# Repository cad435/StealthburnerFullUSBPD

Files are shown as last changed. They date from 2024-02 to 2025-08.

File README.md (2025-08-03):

## Before you download:
 - Update 2024-05-16: I implemented the new and EMI-improved toolhead-boards. However, the "new-EMI" feeders are untested right now. As it is working, I'll only upload the EMI-improved toolhead for now. While manufacturing the new toolheads I also discovered that some of the STM32F072 MCUs I used, are lacking pin 1 markers. It looked to me as if they where sanded down and re-marked (yes I bought them from Aliexpress). I'm not sure if the new EMI-improving did the trick or if some of the MCU's where just faulty. However I do like the new EMI-protection features, so it definately was not a bad investment.
 - Update 2024-07-28 The New Toolheads, together with the "old" Feeders did print for nearly 100h without a single connection-loss. I consider that setup **tested and confirmed working**. A new 3D-Printer in my local makerspace is built right now which will use a "new-EMI" feeder, so that will be also tested in the future.
 - Update 2025-08-02: I now face a different Problem with the setup. **This does affect NEMA14 (round) Steppers together with TMC2130-Drivers.** Standalone-Driver mode is working. Details see here: https://klipper.discourse.group/t/hunting-down-strange-issue-with-extruder-motor/24010. As mentioned by mykepredko on that forum the transistor for heater switching (Q3) is very close on spec as well as obsolete. It is therefore replaced with a CSD17552Q3A, that is well defined within the 3.3V Gate-Voltage.

# StealthburnerFullUSBPD
Two PCB's to connect a Voron Stealthburner Toolhead via USB-PD providing both power and data.

**This has compliant USB-C PD communication, this is not a "hacky" solution where I just shove 20V over the Power-Lines!** <br/>

You can actually charge your Phone, Power your USB-Soldering Iron or whatever you like with it :) <br/>
You can also just use the Feeder Board for whatever non-3D-Printer related USB-PD circuitry you like <br/>

This is aimed at people which are either having some kind of toolchanging system (like me) or are - for whatever reason - changing their toolheads often. Upsides of this project compared to CAN: One cable does it all. Plug it in, it'll work. Well and of course its for people who think USB-C PowerDelivery is cool...<br/><br/>

Konzept_V1 1

Out of my latest Project (Voron 2.4 with toolchanger) I felt the need to simplify connecting Stealthburner-Toolheads to the printer. USB-C PowerDelivery seems suitable. Although it'll only provide 20V to the Toolhead instead of the 24V, it should be good enough.<br/>

I asked around at the Voron-Discord (May 2023), only to find out that there was an attempt by Mellow, but it was taken out of the market. So I sat down and created my own.<br/>

The Project consists of 2 Boards:
 - The "Feeder" PCB which basically integrates some step-Down converter and a USB-PD source IC's
 - The "Toolhead" PCB which consists of an MCU and the neccessary hardware to run fans, heaters, thermistors and the like. <br/><br/>

<p align="center">
 
</p>
<br/><br/>
--> If you use a 4-port USB-Hub, use a half-decent one. I had bad experiences with the 3€ ultra-cheap hubs from Aliexpress, I'm running on a (cheap) Anker-Hub smoothly now. <br/>
<br/>

**Note** that I designed it to be used with 12V Fans (partly because I have loads of 12V Fans laying around). As you need all available airflow you can get, using 12V Fans with 12V seems a better Idea to me that using 24V fans with only 20V as this would mean loosing some power. If the interest is great enough I might add a stepup circuitry to provide 24V for the fans. I don't think its a good idea to step up heater-cartridge voltages as well, as this would mean I need to supply about 3A of current with a step up which generally will generate a considerable amout of heat (same goes for stepping down 20V to 12V). <br/>
<br/>

As of now, the PD power provider IC claim to use e-mark detection for the cables. <br/>
<br/>

Using 24V/40W heater cartridges with 20V will decrease power consumption to about 30W wich (I guess) should be enough for the standard Voron user (not enough though for High-Speed/High-Flow printing etc). That leaves 30W for the stepper-motors, fans etc. (should be plenty enough). Also there are higher power cartridges out there which'll increase power. <br/>
<br/>

**Comment on the Relay switching 5V AUX into the Powerpath:**<br/>
This is actually one of the biggest features of the board - another level of protection for avoiding damage to the printer and possibly other things.
If the heater switching-FET fails and shorts out (zero resistance, actually not uncommon on FET's), the cartridge would heat up indefinately until it fails, ignites or whatever it'll happen. Klipper can't do anything against it, because it will have no hardware controll over the FET and the Heater anymore.<br/>

UNLESS you have another switch to cut off the power - which comes in form of the FET Q1. It'll get switched off from klipper, as Klipper is able to disable the PD-Chip, therefore cutting power completely. However, we don't want to cut power completely, otherwise we can't talk to our MCU anymore an therefore would not be able to restart klipper. So the relay also switches, redirecting the powerpath around the PD-Chip from the "default" Stepdown (5V) to the toolhead. So we just "switch" power to another safe Level (5V). With 5V the heater doesn't have enough power to get seriously hot (I tested, it merely gets 50C hot).

Licensed under Open Source Hardware Association license https://www.oshwa.org/definition/

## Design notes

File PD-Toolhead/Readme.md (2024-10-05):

Update 2024-10-05: I accidentlly left R7 and R8 as 100R series resistance for the USB-Lines. This seemes to be working good for my main Printer <br>
For another setup however, I encountered problems. After a while I found 100R to be too much resistance. Therefore I replaced it with 0R default. <br>
If you find yourself to have random disconnects I advice you to increase those values (20R should be enough!) <br>
However I believe that the 2.2kR@100Mhz Common-Mode chocke (FL1) should be more than enough. <br> <br>

I found it working with all the Ferrite beads (L1/L4/L5) beeing only ~300R@100Mhz, as well as the common-mode choke beeing just ~600R@100Mhz. <br> <br>

Use two M2 brass inserts on the 2 holes beside the USB-C Connector. <br> <br>



The holes where the "unknurled" shoulder is fitted is 3.1mm in diameter 
Brass inserts I used are sold as "OD=3.5mm, Lenght=3mm". The critical measurement is denoted as "dk" in the picture below.



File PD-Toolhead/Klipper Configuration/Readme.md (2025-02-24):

# Klipper Configuration

Inside the provided Klipper_Toolhead.cfg there are only the lines written down which are tied to the hardware. <br>
Anything else (PID values, min temp, max temp for example) is setup specific. See https://www.klipper3d.org/Config_Reference.html for aditional information<br>

For the compile config, consider setting PB9 in GPIO pins (see Image below). <br>
This will spin up the fan connected to the bottom fan-connector (usually the fan for the Heatsink!) <br>
If anything happens during the print and the printer changes into error-mode, then your hotend (more specific the coldend/heatsink) will not overheat.

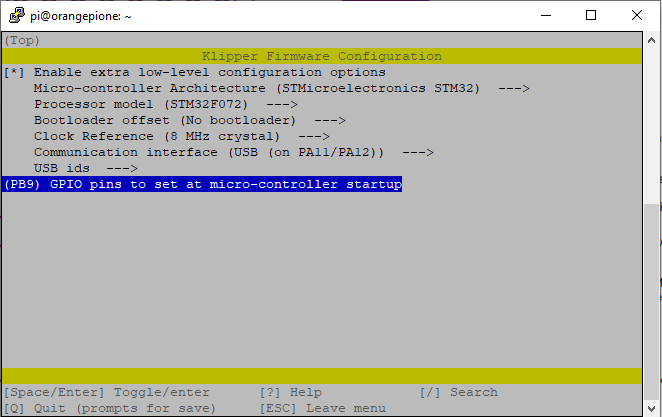
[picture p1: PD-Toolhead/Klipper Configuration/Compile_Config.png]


---

## Flashing with KIAUH v6:
KIAUH v6 has the ability to save compile configs.
 - download pd-hotend-stm32f072.config
 - place it inside /home/usr/klipper-kconfigs/ folder<br>
    (replace usr with your klipper user. On a standard installation this would be "pi" --> /home/pi/klipper-kconfigs/)
 - restart KIAUH v6 and navigate to the "Advanced"-Menu to get the firmware flashing Menu
 - when try to build or build+flash KIAUH should present you the option to load the config.

You also don't have to place the board in bootloader mode anymore. When flashing with KIAUH just select "connected via USB". The flash utility of KIAUH will place the board into bootloader-mode on its own. <br>
I'm not exactly sure since when this is possible. My setup runs with KIAUH v6 and Klipper v0.12.0. <br><br>

Be aware, that KIAUH may state a failed flash although flashing actually succeeds.<br>
Inside your command-Line you are looking for the lines:
```
[...]

Download        [=========================] 100%        36988 bytes
Download done.
File downloaded successfully
Submitting leave request...

[...]

```

See this post for additional reference:
https://github.com/dw-0/kiauh/issues/545#issuecomment-2395065270

---

## "Legacy" Flashing:

Hold down the "BOOT" button (see Pin Description PDF), than press the RESET Button. The Toolhead will be accessible via ST's USB-Hardware Bootloader in DFU. Use "USB (DFU mode)" option in KIAUH.

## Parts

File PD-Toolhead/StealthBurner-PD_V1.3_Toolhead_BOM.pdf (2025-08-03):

Comment | Description | Value | Designator | Footprint | Quantity
LM1117IMPX-3.3/NOPB | +3,3V LDO LM1117MP-3.3 | | A1 | SOT230P700X1.80-4N | 1
100nF | CAP-CER 100n 50V 10% SMD 0603 X7R | | C1, C2, C3, C4, C5, C19, C20, C23, C24, C27, C30 | CAPC1608X0.95N_0603 | 11
1µF | CAP-CER 1u 16V 10% SMD 0603 X7R | | C6, C7, C8, C17, C25, C26 | CAPC1608X0.95N_0603 | 6
10µF | CAP-CER 10u 25V 10% SMD 1206 X7R | | C9, C13, C14, C15, C16, C18, C21, C22, C31 | CAPC3216X1.80N_1206 | 9
100µF | CAP-ELC 100u 25V 20% SMD D6.3mm H7.7mm R4.4mm | | C10 | CAPAE660X8.00N_D8 | 1
18pF | CAP-CER 18p 50V 5% SMD 0603 C0G | | C11, C12 | CAPC1608X0.87N_0603 | 2
100pF | CAP-CER 100p 50V 5% SMD 0603 C0G | | C28, C29 | CAPC1608X0.87N_0603 | 2
SS1FL3HM3/H | DIO-SKY 30V 420mV 1A SMD DO-219AB SS1FL3HM3/H | | D1, D2 | SODFL3718X1.08N_DO-219AB | 2
2 Pin male | 2 Pin male | | FAN0, FAN1, Thermistor | JST_B2B-XH-A(LF)(SN) | 3
2.2kR @ 100MHz / 1206 | 2 Line Common Mode Choke 1206 | | FL1 | Common Mode Choke 1206 | 1
Terminalblock X2 | | | Heater | TerminalblockX2 | 1
JP1X4 | 4 Pin PFOSTENSTECKER, Fastermaß 2,54mm | | I2C, P2, P3 | P1x4-R2.54-X0.67 | 3
STM32F072C8T6 | Integrated Circuit | | IC1 | QFP50P900X900X160-48N | 1
ME3116 | 1A up to 40V Input Step-Down DC/DC Regulator | | IC2, IC3 | SOT23-6 | 2
Switch Black | Tactile Switch | | J1 | Tactile_SW_2Pins | 1
Switch Red | Tactile Switch | | J2 | Tactile_SW_2Pins | 1
USB 3.1 C Receptacle | USB 3.1 Type C Receptacle Horizontal THR WR-COM | | J3 | C165948 | 1
Ferrite_Bead | Ferrite_Bead | 600R @ 1MHz | L1, L4, L5 | 0603 | 3
Inductor | Inductor | 4.7uH/1.7A/1210 | L2, L3 | 5.2x4mm | 2
LED-0603 GN LC | LED WÜRTH 2mA 150060VS75000 | | LD1, LD2, LD3 | LEDC1608X0.80N_0603 | 3
3 Pin male | 3 Pin male | | LED | JST_B3B-XH-A(LF)(SN) | 1
JST-XH | 4 Pin male | | MOT | JST_B4B-XH-A(LF)(SN) | 1
Marker IPC7351 | Fiducial Marker IPC7351 Diameter 1.5mm, Clearance Diameter 3mm | | MP1, MP2, MP3, MP4, MP5, MP6 | PCB-Marker_IPC7351 | 6
JP1X3 | 3 PIN PFOSTENSTECKER, Rastermaß 2,54mm | | P4 | P1x3-R2.54-X0.63 | 1
CSD17552Q3A | N-MOSFET LOW RDSon | | Q1, Q2, Q3 | SON67P300X300X1.00-9N | 3
10k | RES 10k 1% 100mW TK100 SMD 0603 G | | R1, R2, R3, R10, R18, R20, R21, R26, R27, R32, R33, R34, R36 | RESC1608X0.55N_0603 | 13
0 | RES 0R 5% 100mW TK100 SMD 0603 G | | R6, R7, R8 | RESC1608X0.55N_0603 | 3
100k | RES 100k 1% 100mW TK100 SMD 0603 G | | R9, R25 | RESC1608X0.55N_0603 | 2
1k | RES 1k 1% 100mW TK100 SMD 0603 G | | R11, R12, R35 | RESC1608X0.55N_0603 | 3
100 | RES 100R 1% 100mW TK100 SMD 0603 G | | R14, R16, R17, R24, R37, R38 | RESC1608X0.55N_0603 | 6
470k | RES 470k 1% 100mW TK100 SMD 0603 G | | R22 | RESC1608X0.55N_0603 | 1
680R | RES 680R 1% 100mW TK100 SMD 0603 G | | R23 | RESC1608X0.55N_0603 | 1
4.7k | RES 4k7 1% 100mW TK100 SMD 0603 G | | R28, R29, R30 | RESC1608X0.55N_0603 | 3
P1X6-R2.54mm-V-X9.5mm | P1X6-R2.54mm-V-X9.5mm-Modu II Stiftleiste | | SPI | P1X6-R2.54-V-X9.5 | 1
TMC2130BREAKOUT | | | TMC1 | TMC2130BREAKOUT | 1
CH224K | USB PD and Other Fast Charging Protocol Sink Controller | Value | U1 | ESSOP100P600X180_E P-11N | 1
XTAL_8MHz | Crystal | | Y1 | SMD-3225_4P | 1

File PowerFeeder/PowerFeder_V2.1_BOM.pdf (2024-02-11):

Comment | Description | Value | Designator | Footprint | Quantity
100µF | CAP-ELC 100u 25V 20% SMD D6.3mm H7.7mm R4.4mm | | C1, C6, C17 | CAPAE660X8.00N_D8 | 3
100nF | CAP-CER 100n 50V 10% SMD 0603 X7R | | C4, C7, C8, C9, C10, C11, C12, C13 | CAPC1608X0.95N_0603 | 8
10µF | CAP-CER 10u 25V 10% SMD 1206 X7R | | C14 | CAPC3216X1.80N_1206 | 1
V8PAM10S | DIO-SKY 100V 840mV 8A SMD DO-221BC-2 V8PAM10S | | D1, D3, D5 | DO-221BC | 3
6.3A 250V | NResettable, 6.3A, 250V, SMD UMT250 | | F1 | FUSC10030X3.00N | 1
120 | FERRIT-BEAD-120R-3A-1206 | | FB1, FB2 | INDC3216X1.30N_1206 | 2
USB 3.1 C Receptacle | USB 3.1 Type C Receptacle Horizontal THR WR-COM | | J1, J2 | C165948 | 2
Terminalblock X2 | | | J3, J4, J5 | TerminalblockX2 | 3
Inductor | Inductor | 15uH | L1 | 12x12_L-Footprint | 1
Marker IPC7351 | Fiducial Marker IPC7351 Diameter 1.5mm, Clearance Diameter 3mm | | MP1, MP2, MP3, MP4, MP5, MP6 | PCB-Marker_IPC7351 | 6
NCE3080 | NCE N-Channel Enhancement Mode Power MOSFET | | Q1 | NCE3080 | 1
SI2318CDS-T1-GE3 | N-MOSFET SI2318CDS-T1-GE3 | | Q2, Q3 | SOT95P240X1.10-3N_SOT-23 | 2
0 | RES 0R 250mW SMD 1206 G | | R1, R14, R19, R24, R38 | RESC3216X0.65N_1206 | 5
1.5k | RES 1k5 1% 100mW TK100 SMD 0603 G | | R8, R12, R18, R20 | RESC1608X0.55N_0603 | 4
Res | Resistor | 5m | R13 | R2512 | 1
100k | RES 100k 1% 100mW TK100 SMD 0603 G | | R15, R16, R23 | RESC1608X0.55N_0603 | 3
33K | RES 33k 1% 100mW TK100 SMD 0603 G | | R17 | RESC1608X0.55N_0603 | 1
10k | RES 10k 1% 100mW TK100 SMD 0603 G | | R22, R26, R27, R28, R29, R31, R32, R33, R34, R35, R36 | RESC1608X0.55N_0603 | 11
Relay, SRA-xVDC-CL | | | S1 | SRA-24VDC-CL | 1
RT8289 | Buck Step Down Regulator with 5.5 to 36 V Input and 1.23 to 31 V Output, -40 to 125 degC, 8-Pin SOIC (D), Green (RoHS & no Sb/ Br) | | U2 | SOP8-EP | 1
TPS25740B | | | U3 | QFN-24_EP | 1

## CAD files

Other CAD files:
PD-Toolhead/USB_Cable_Holder.f3z

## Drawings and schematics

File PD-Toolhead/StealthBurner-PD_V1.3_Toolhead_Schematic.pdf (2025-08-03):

C10
100µF

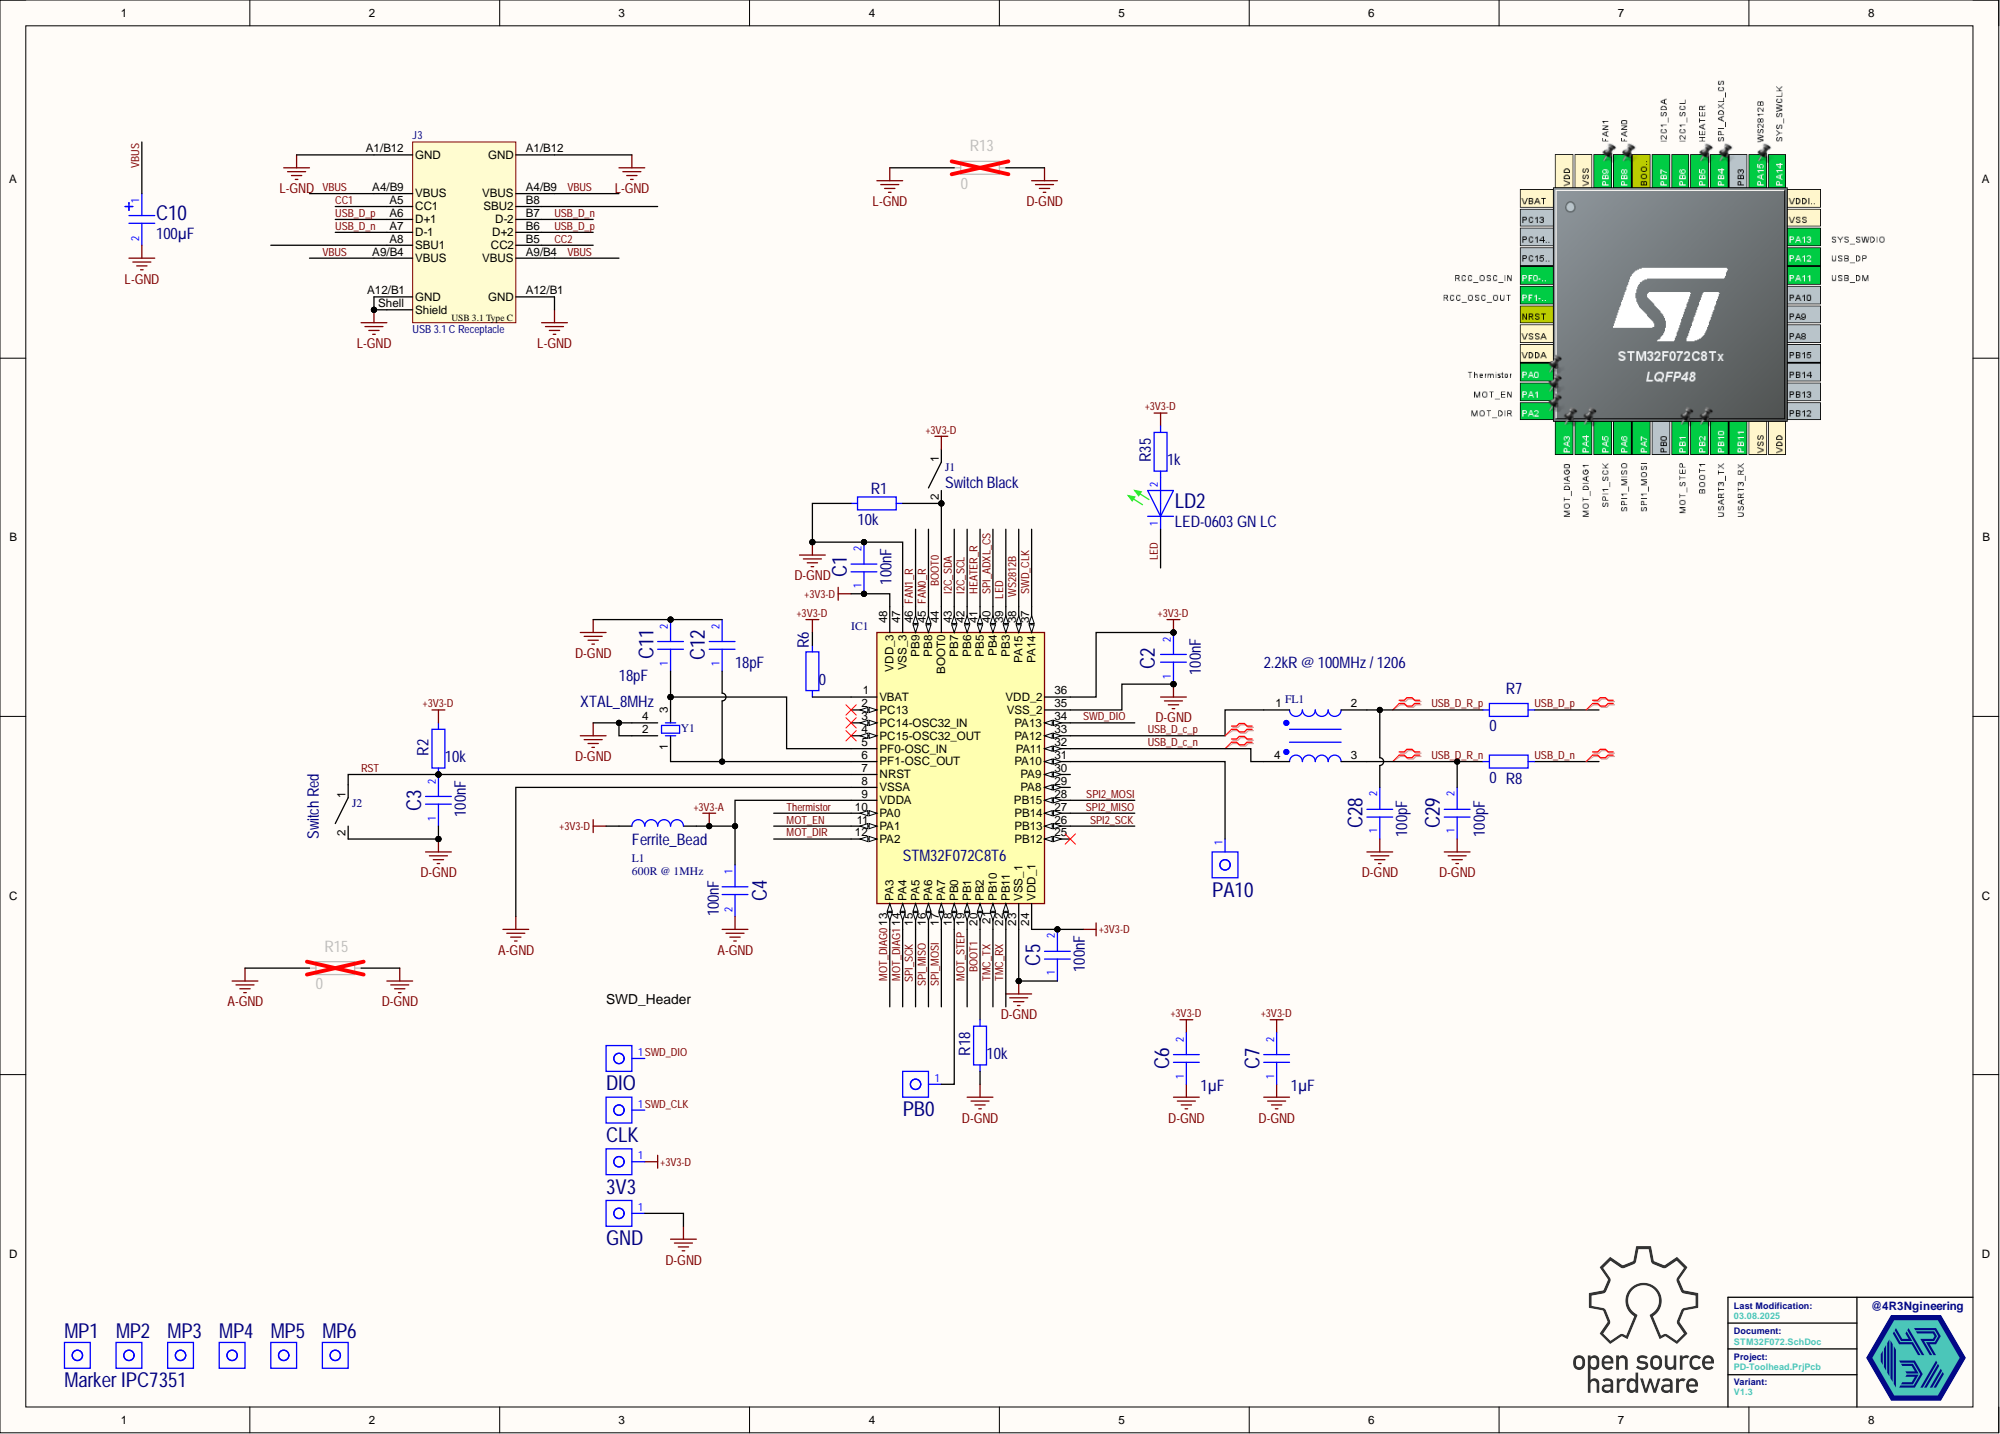
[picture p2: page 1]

## Ferrite_Bead +3V3-TMC

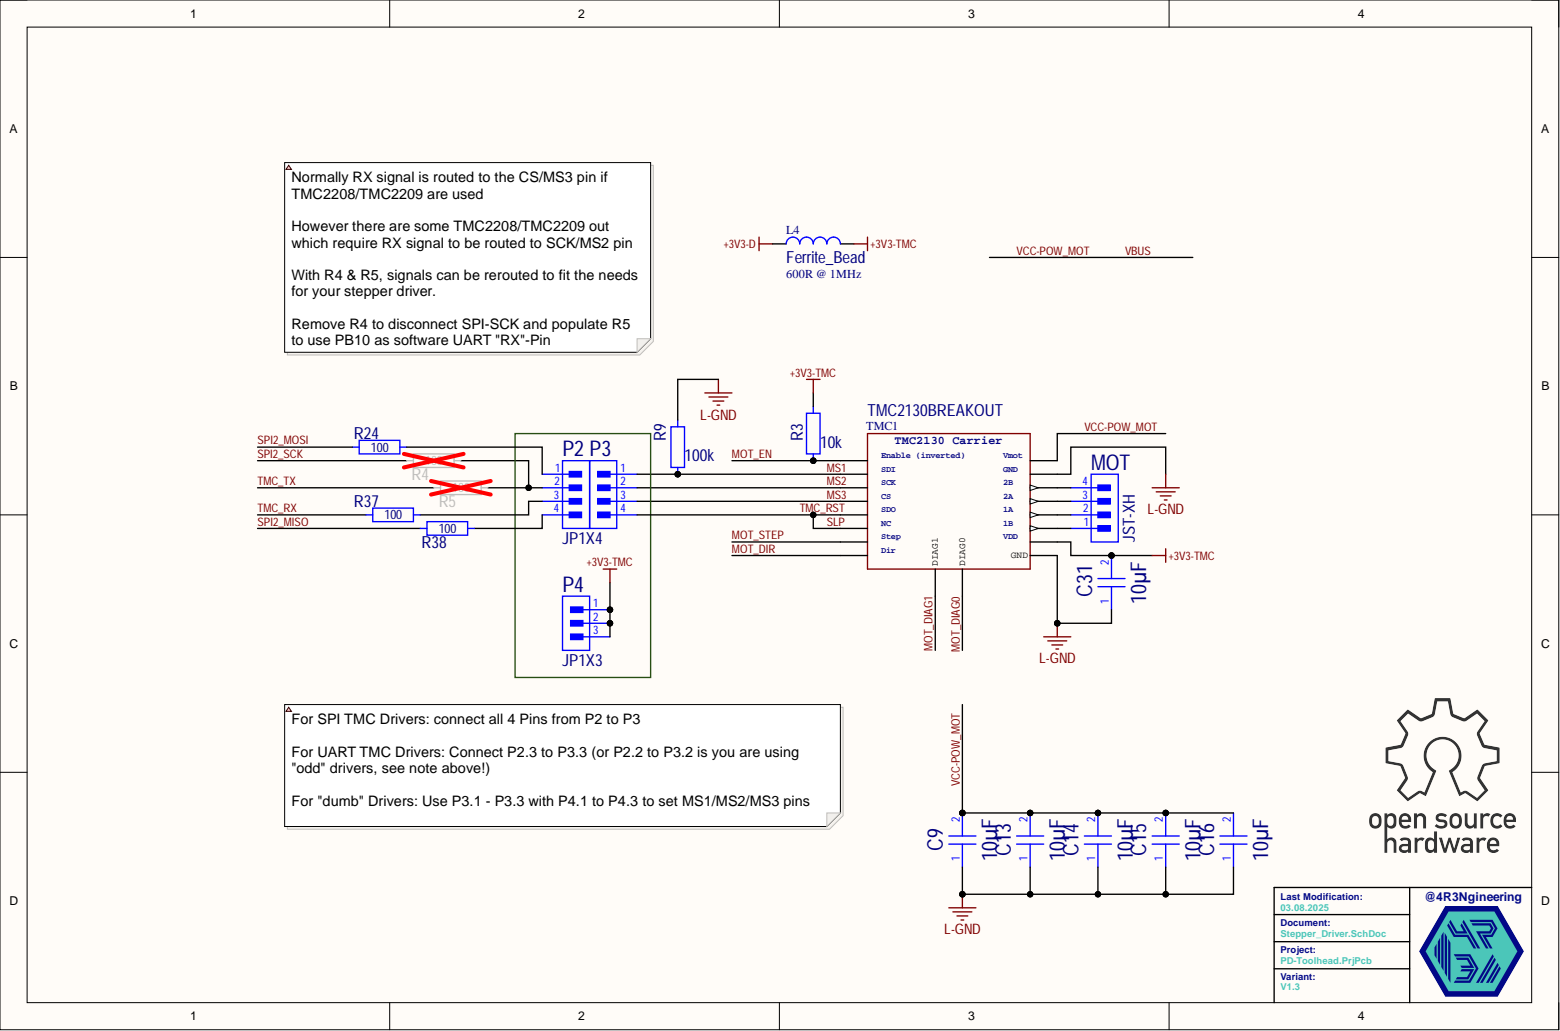
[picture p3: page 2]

Normally RX signal is routed to the CS/MS3 pin if
TMC2208/TMC2209 are used

However there are some TMC2208/TMC2209 out
which require RX signal to be routed to SCK/MS2 pin

With R4 & R5, signals can be rerouted to fit the needs
for your stepper driver.

Remove R4 to disconnect SPI-SCK and populate R5
to use PB10 as software UART "RX"-Pin

For SPI TMC Drivers: connect all 4 Pins from P2 to P3

For UART TMC Drivers: Connect P2.3 to P3.3 (or P2.2 to P3.2 is you are using
"odd" drivers, see note above!)

For "dumb" Drivers: Use P3.1 - P3.3 with P4.1 to P4.3 to set MS1/MS2/MS3 pins

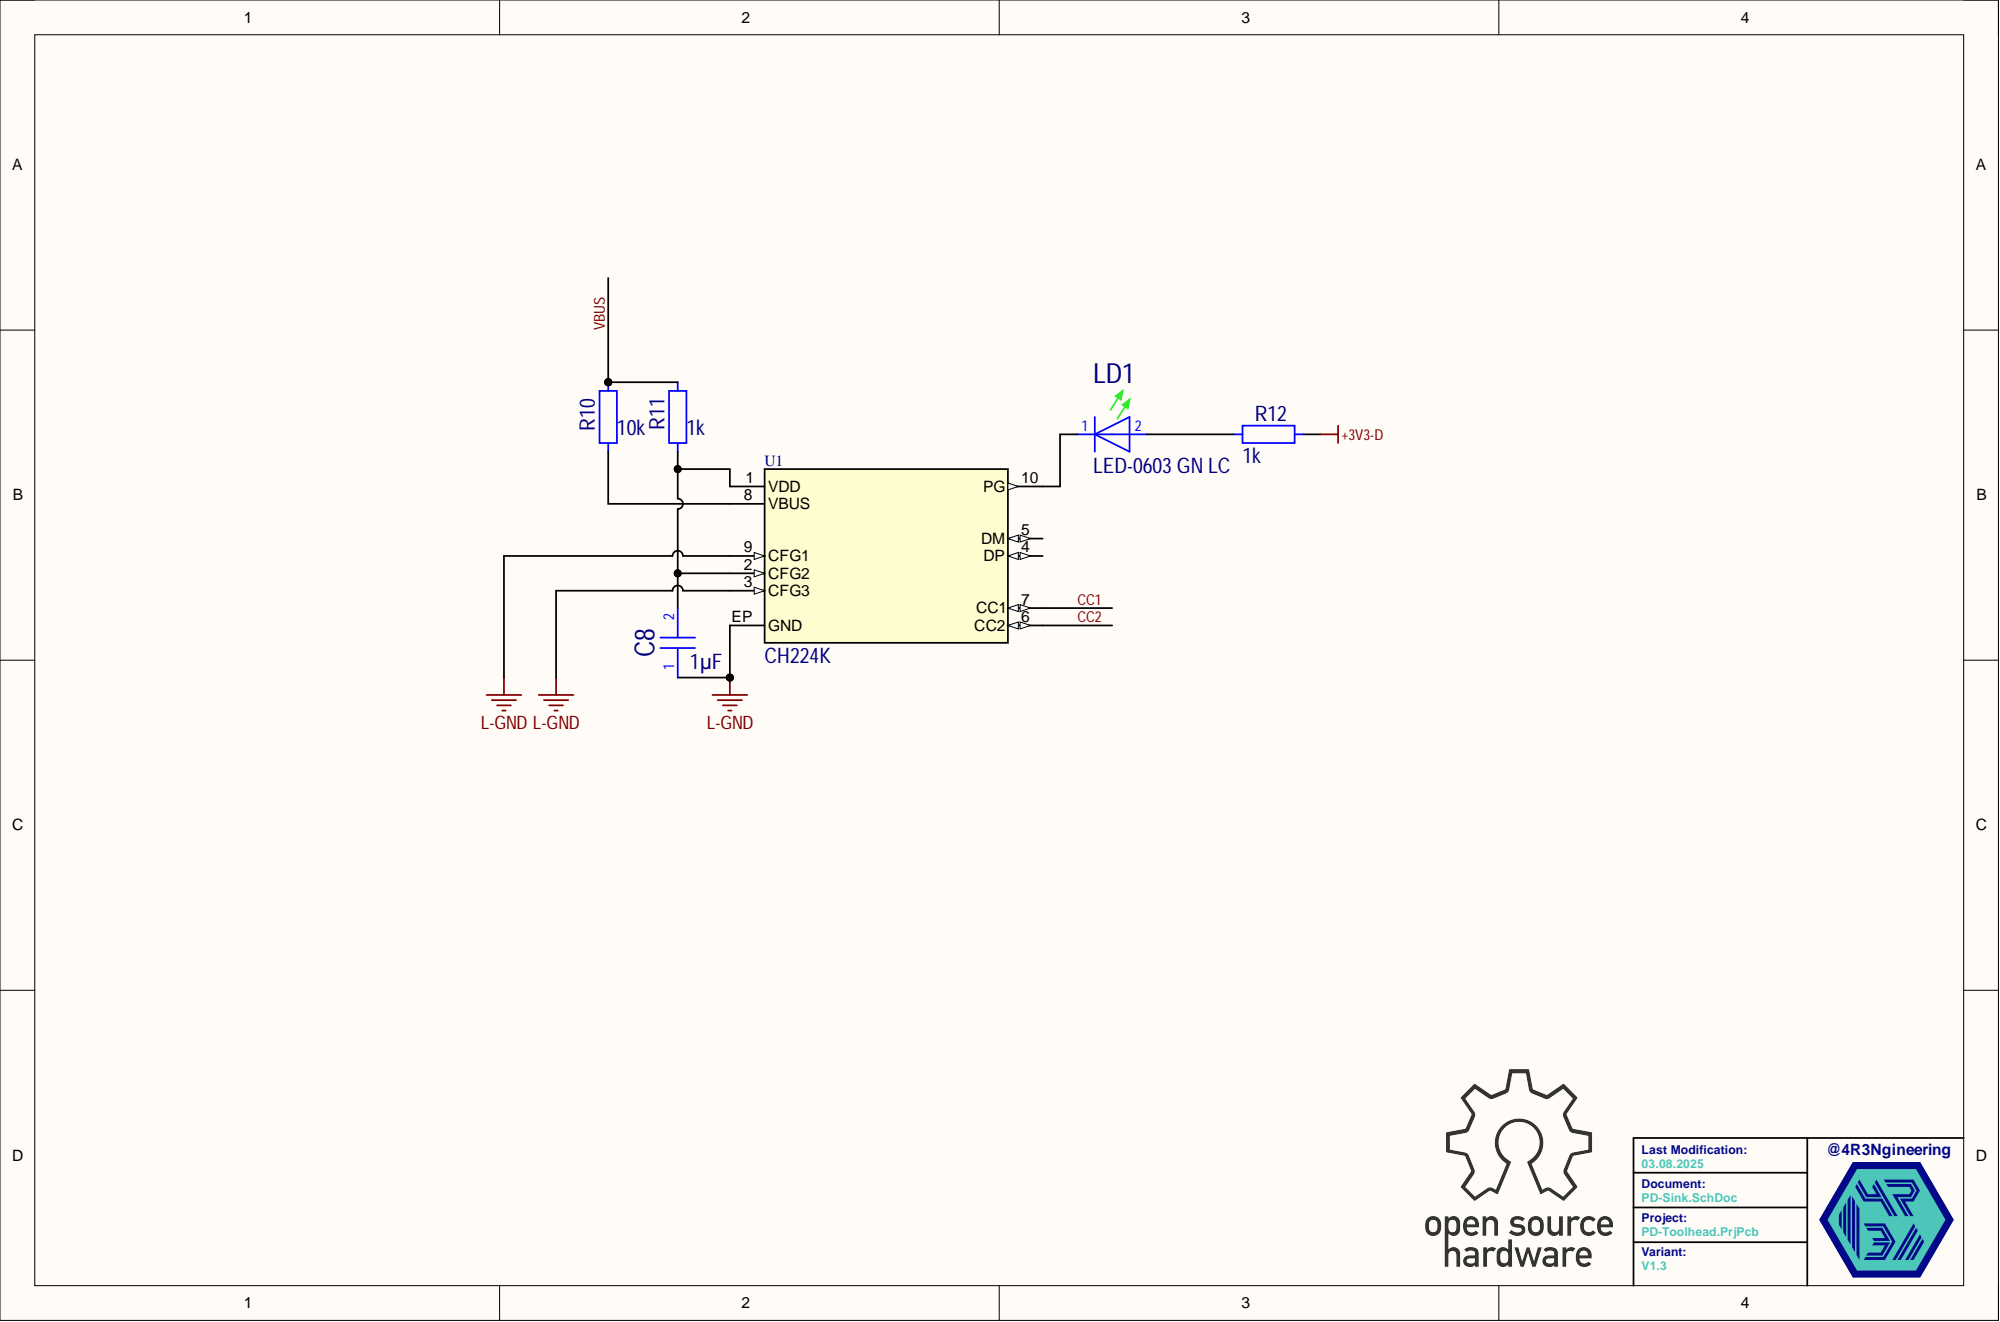
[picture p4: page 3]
st Modific; ation:; Docum; ent: PD-Sink.SchDoc; Proje; ct: PD-Toolhe; ad.PrjPc; ariant:; VBU; VBUS R10; LED-0603

# Inductor ⁴.7uH/1.7A/

## Inductor

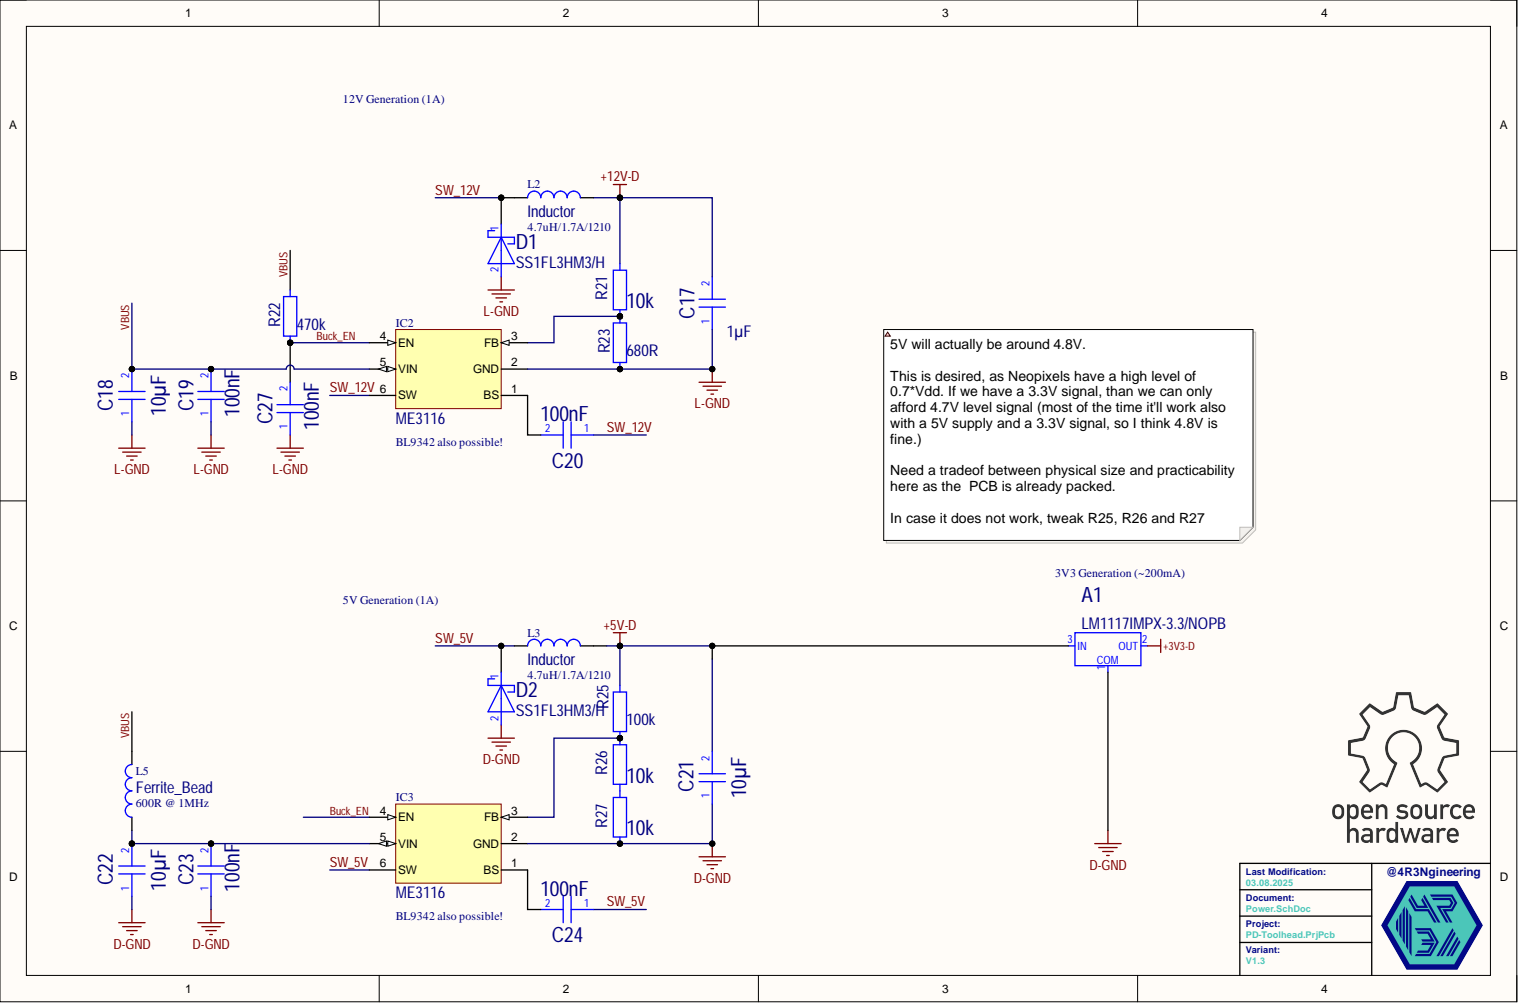
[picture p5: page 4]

5V will actually be around 4.8V

This is desired, as Neopixels have a high level of
Vdd. If we have a 3.3V signal, than we can only
afford 4.7V level signal (
with a 5V supply and a 3.3V signal, so I think 4.8V is
fine.)

most of the time it'll work also

Need a tradeof between physical size and practicability
here as the PCB is already packed.

In case it does not work, tweak R25, R26 and R27

# FAN0

## 2 Pin male

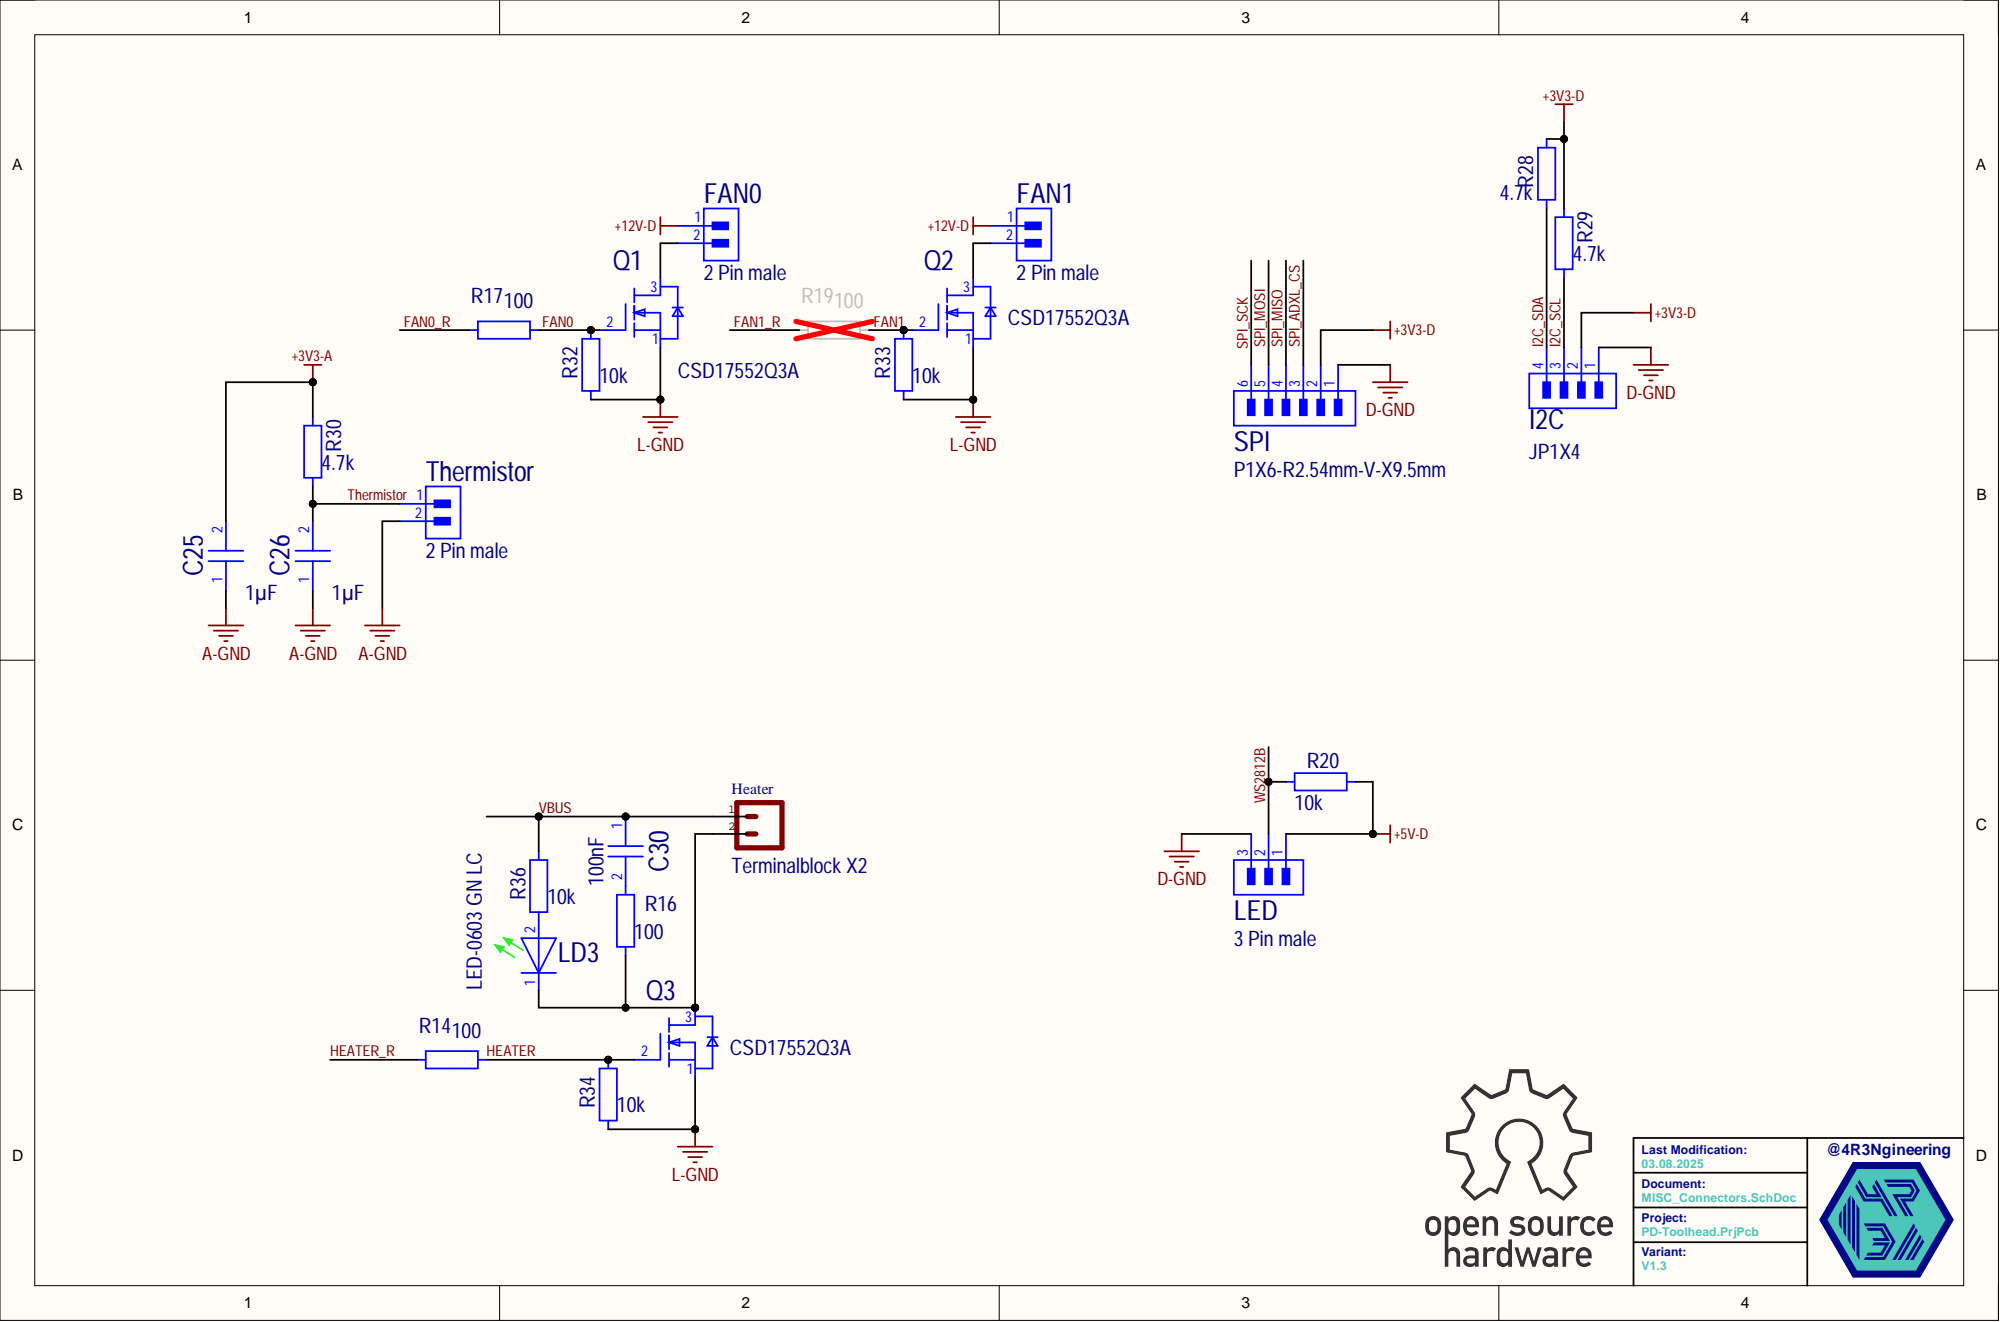
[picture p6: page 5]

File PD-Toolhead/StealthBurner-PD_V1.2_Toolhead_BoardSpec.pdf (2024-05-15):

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
PCB Name
Size
Attached Layerstack mandatory Layers
Thickness
Material
Copper-Thickness top/bottom Copper-Thickness inner layers Surface
Solder mask
Peelable mask
Scoring
UL required
Outline/Shape
Chamfer
Electrical Test
Impedance
IPC/Perfag
internal millings
Silkscreen Top
Silkscreen Bottom
Pressfit

PD-Toolhead
Xmm x Xmm (see drawing)
no4

1.6mm
FR4 / Epoxy
35µm
17.5µm
chemical Ni/Au
double-sided (black or matte-black) no
no
no
milling
no
yes
no
Class 2
yes
yes
yes
no

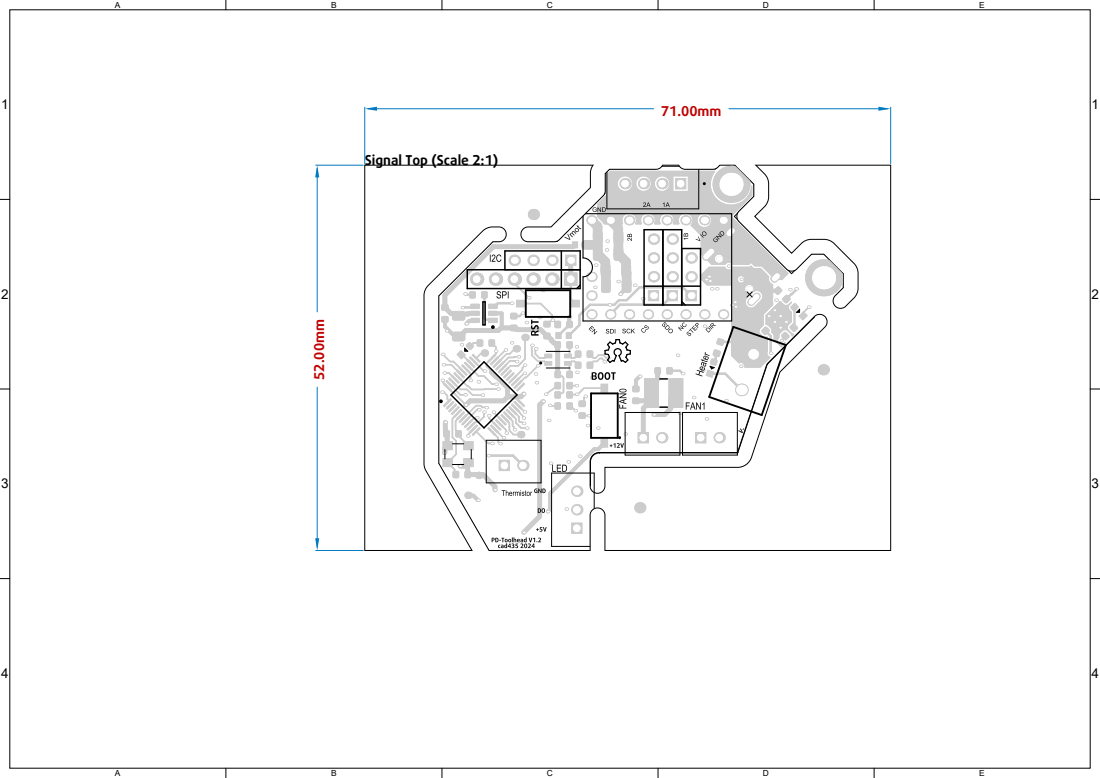
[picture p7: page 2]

Signal Top (Scale 2:1)

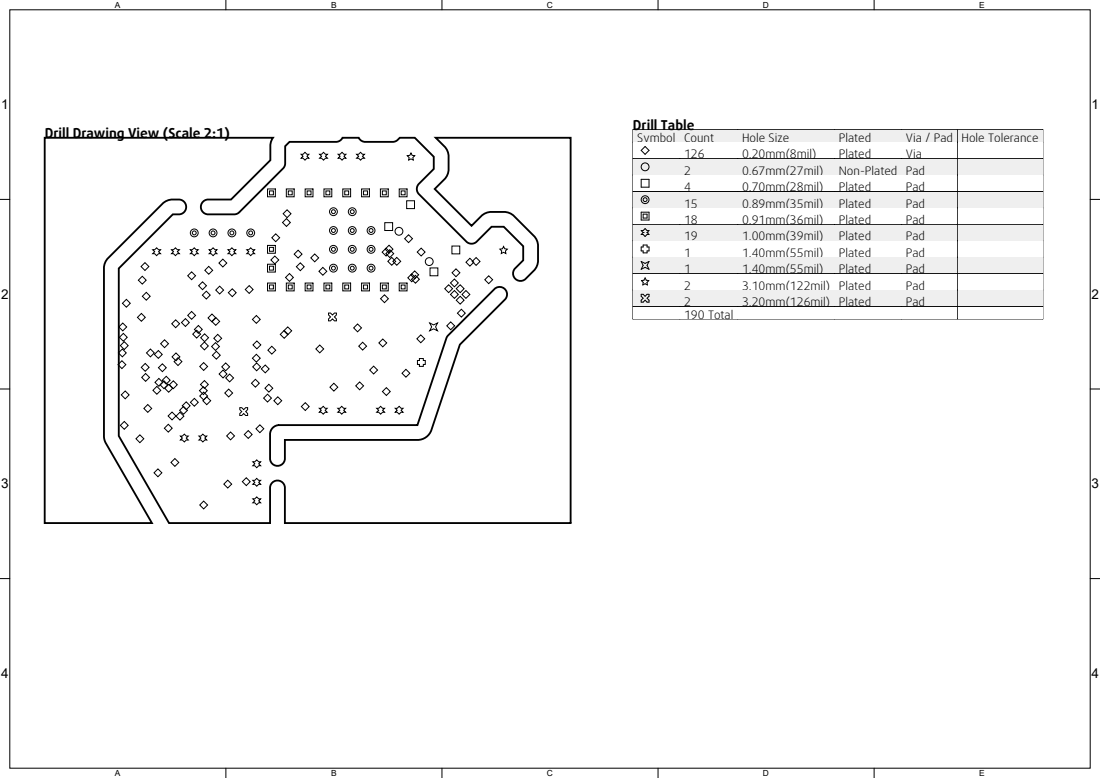
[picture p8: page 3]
Drill Table

Drill Drawing View (Scale 2:1)

Symbol | Count | Hole Size | Plated | Via / Pad | Hole Tolerance
126 | 0.20mm(8mil) | Plated | Via
2 | 0.67mm(27mil) | Non-Plated | Pad
4 | 0.70mm(28mil) | Plated | Pad
15 | 0.89mm(35mil) | Plated | Pad
18 | 0.91mm(36mil) | Plated | Pad
19 | 1.00mm(39mil) | Plated | Pad
1 | 1.40mm(55mil) | Plated | Pad
2 | 3.10mm(122mil) | Plated | Pad
2 | 3.20mm(126mil) | Plated | Pad
190 Total

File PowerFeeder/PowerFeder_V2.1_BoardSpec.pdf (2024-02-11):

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
VX Instruments Part Number Size
Attached Layerstack mandatory Layers
Thickness
Material
Copper-Thickness top/bottom Copper-Thickness inner layers Surface
Solder mask
Peelable mask
Scoring
UL required
Outline/Shape
Chamfer
Electrical Test
Impedance
IPC/Perfag
internal millings
Silkscreen Top
Silkscreen Bottom
Pressfit

PD-PowerFeeder
Xmm x Xmm (see drawing)
yes 2

1.6mm
FR4 / Epoxy
35µm (see layer stack)
35µm (see layer stack)
chemical Ni/Au
double-sided (black or matte-black) no
no
no
milling
no
yes
no
Class 2
yes
yes
yes
no

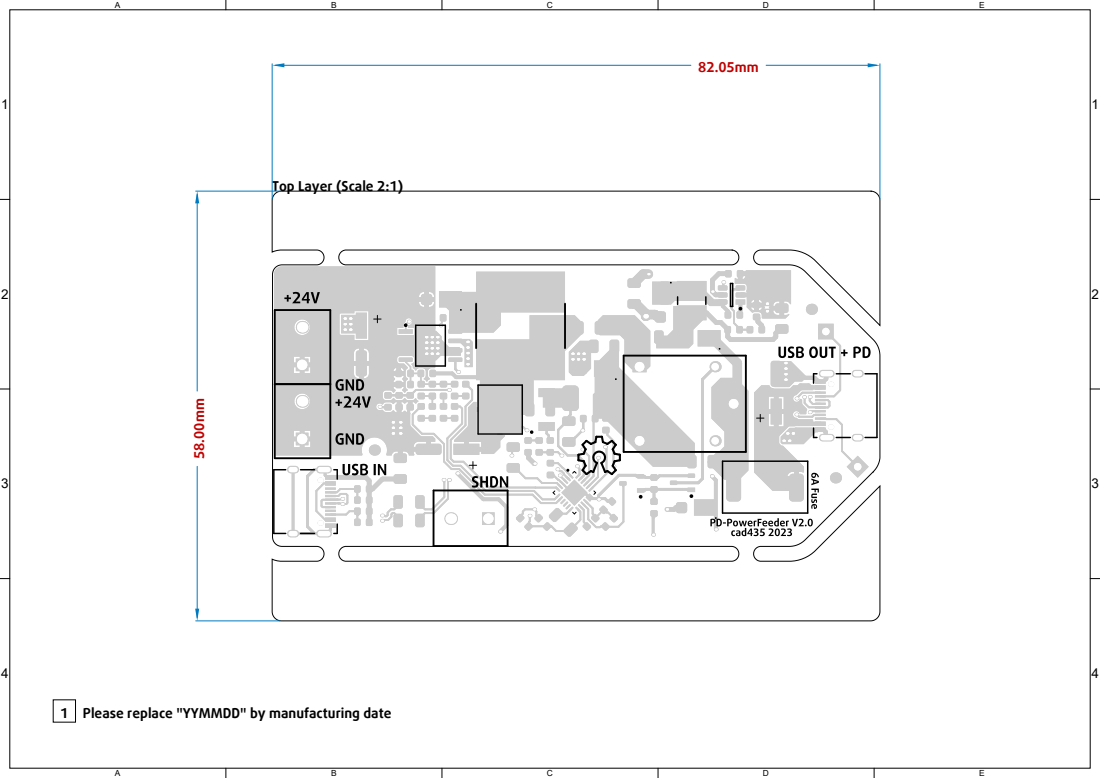
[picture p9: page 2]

Top Layer (Scale 2:1)

1 Please replace "YYMMDD" by manufacturing date

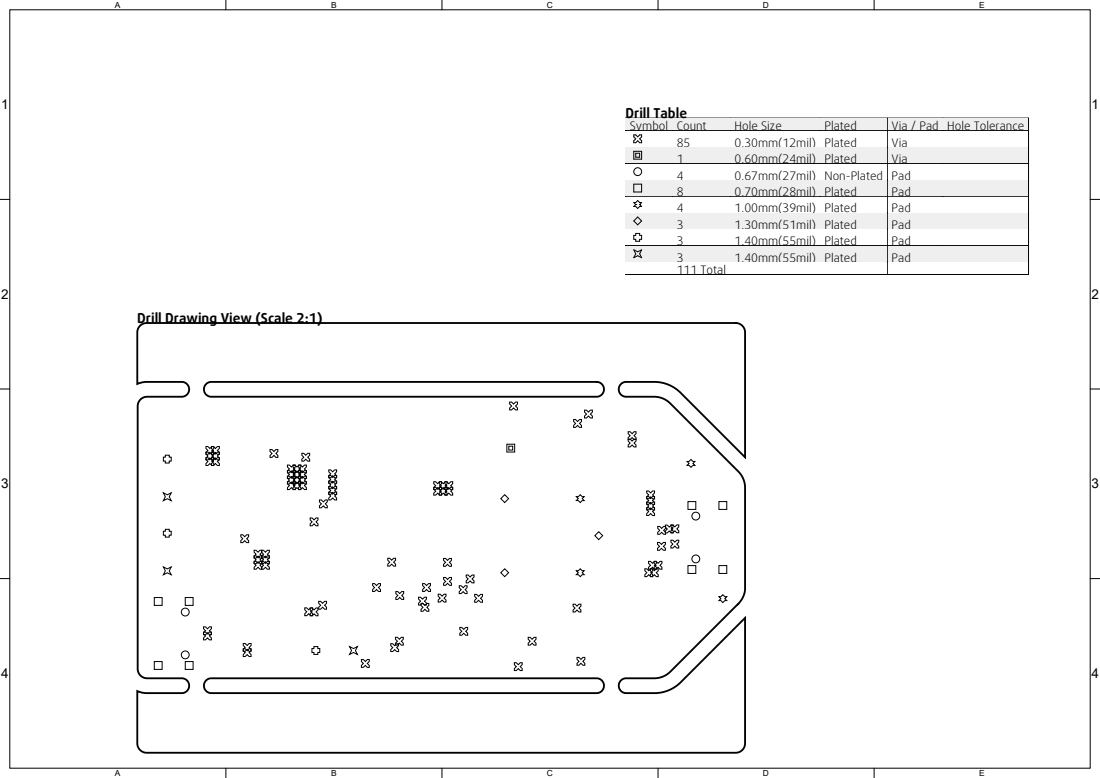
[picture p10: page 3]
Drill Table

Symbol | Count | Hole Size | Plated | Via / Pad | Hole Tolerance
85 | 0.30mm(12mil) | Plated | Via
1 | 0.60mm(24mil) | Plated | Via
4 | 0.67mm(27mil) | Non-Plated | Pad
8 | 0.70mm(28mil) | Plated | Pad
4 | 1.00mm(39mil) | Plated | Pad
3 | 1.30mm(51mil) | Plated | Pad
3 | 1.40mm(55mil) | Plated | Pad
111 Total

Drill Drawing View (Scale 2:1)

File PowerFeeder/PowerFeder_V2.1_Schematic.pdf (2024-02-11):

P1

TP 1

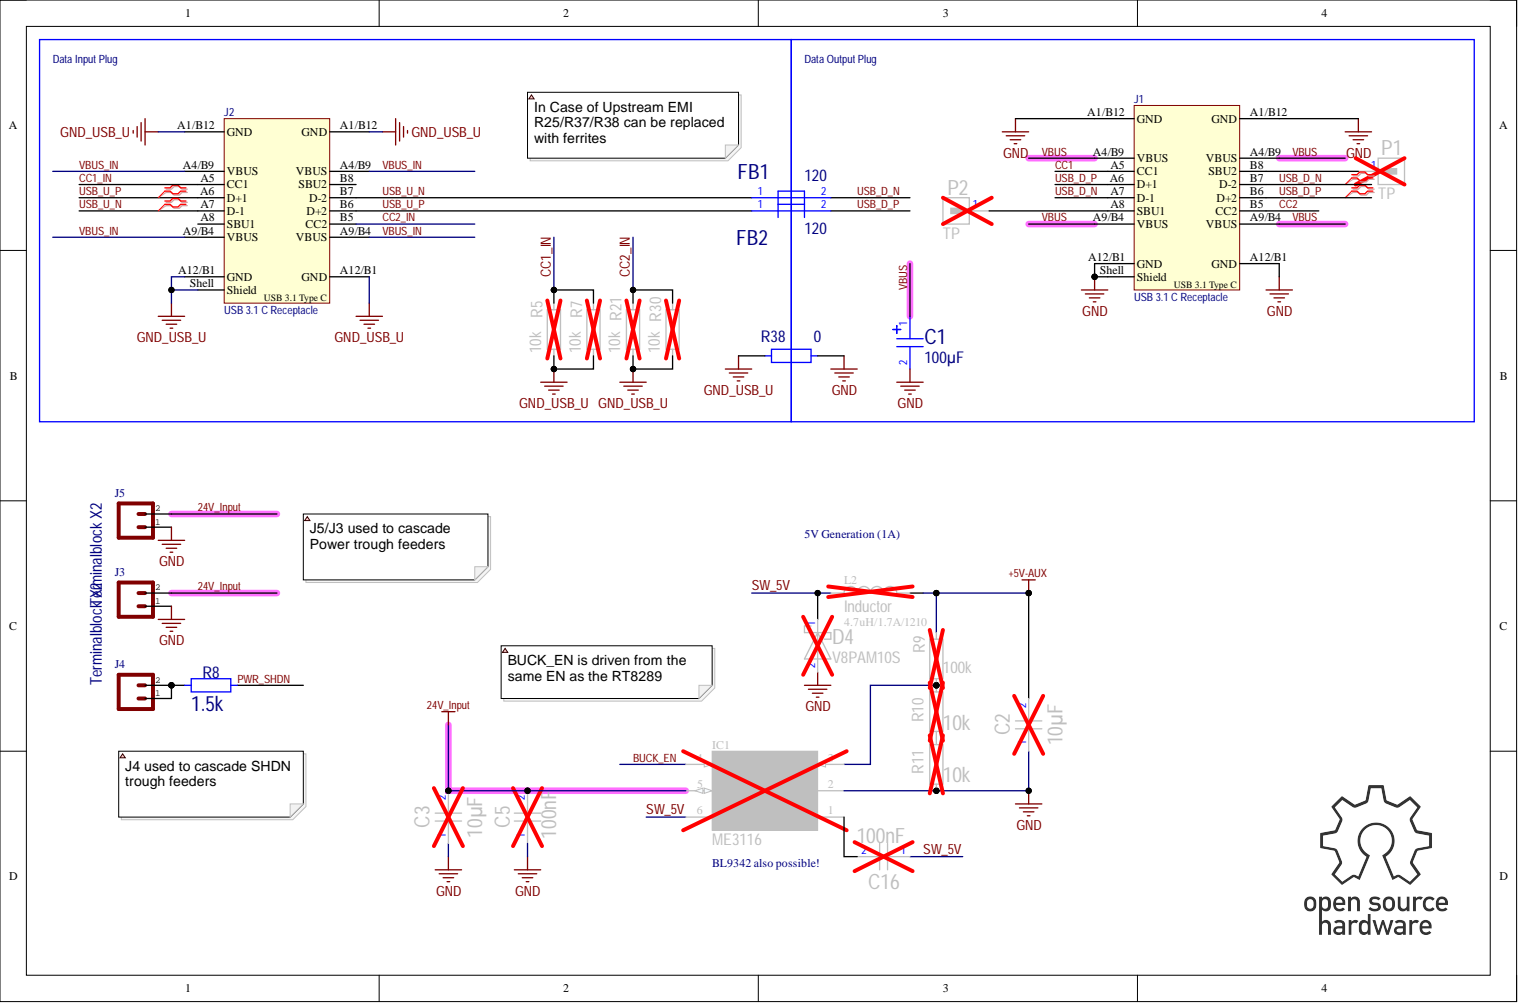
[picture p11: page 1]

In Case of Upstream EMI
R25/R37/R38 can be replaced
with ferrites

BUCK_EN is driven from the
same EN as the RT8289

J4 used to cascade SHDN
trough feeders

RT8289

100k

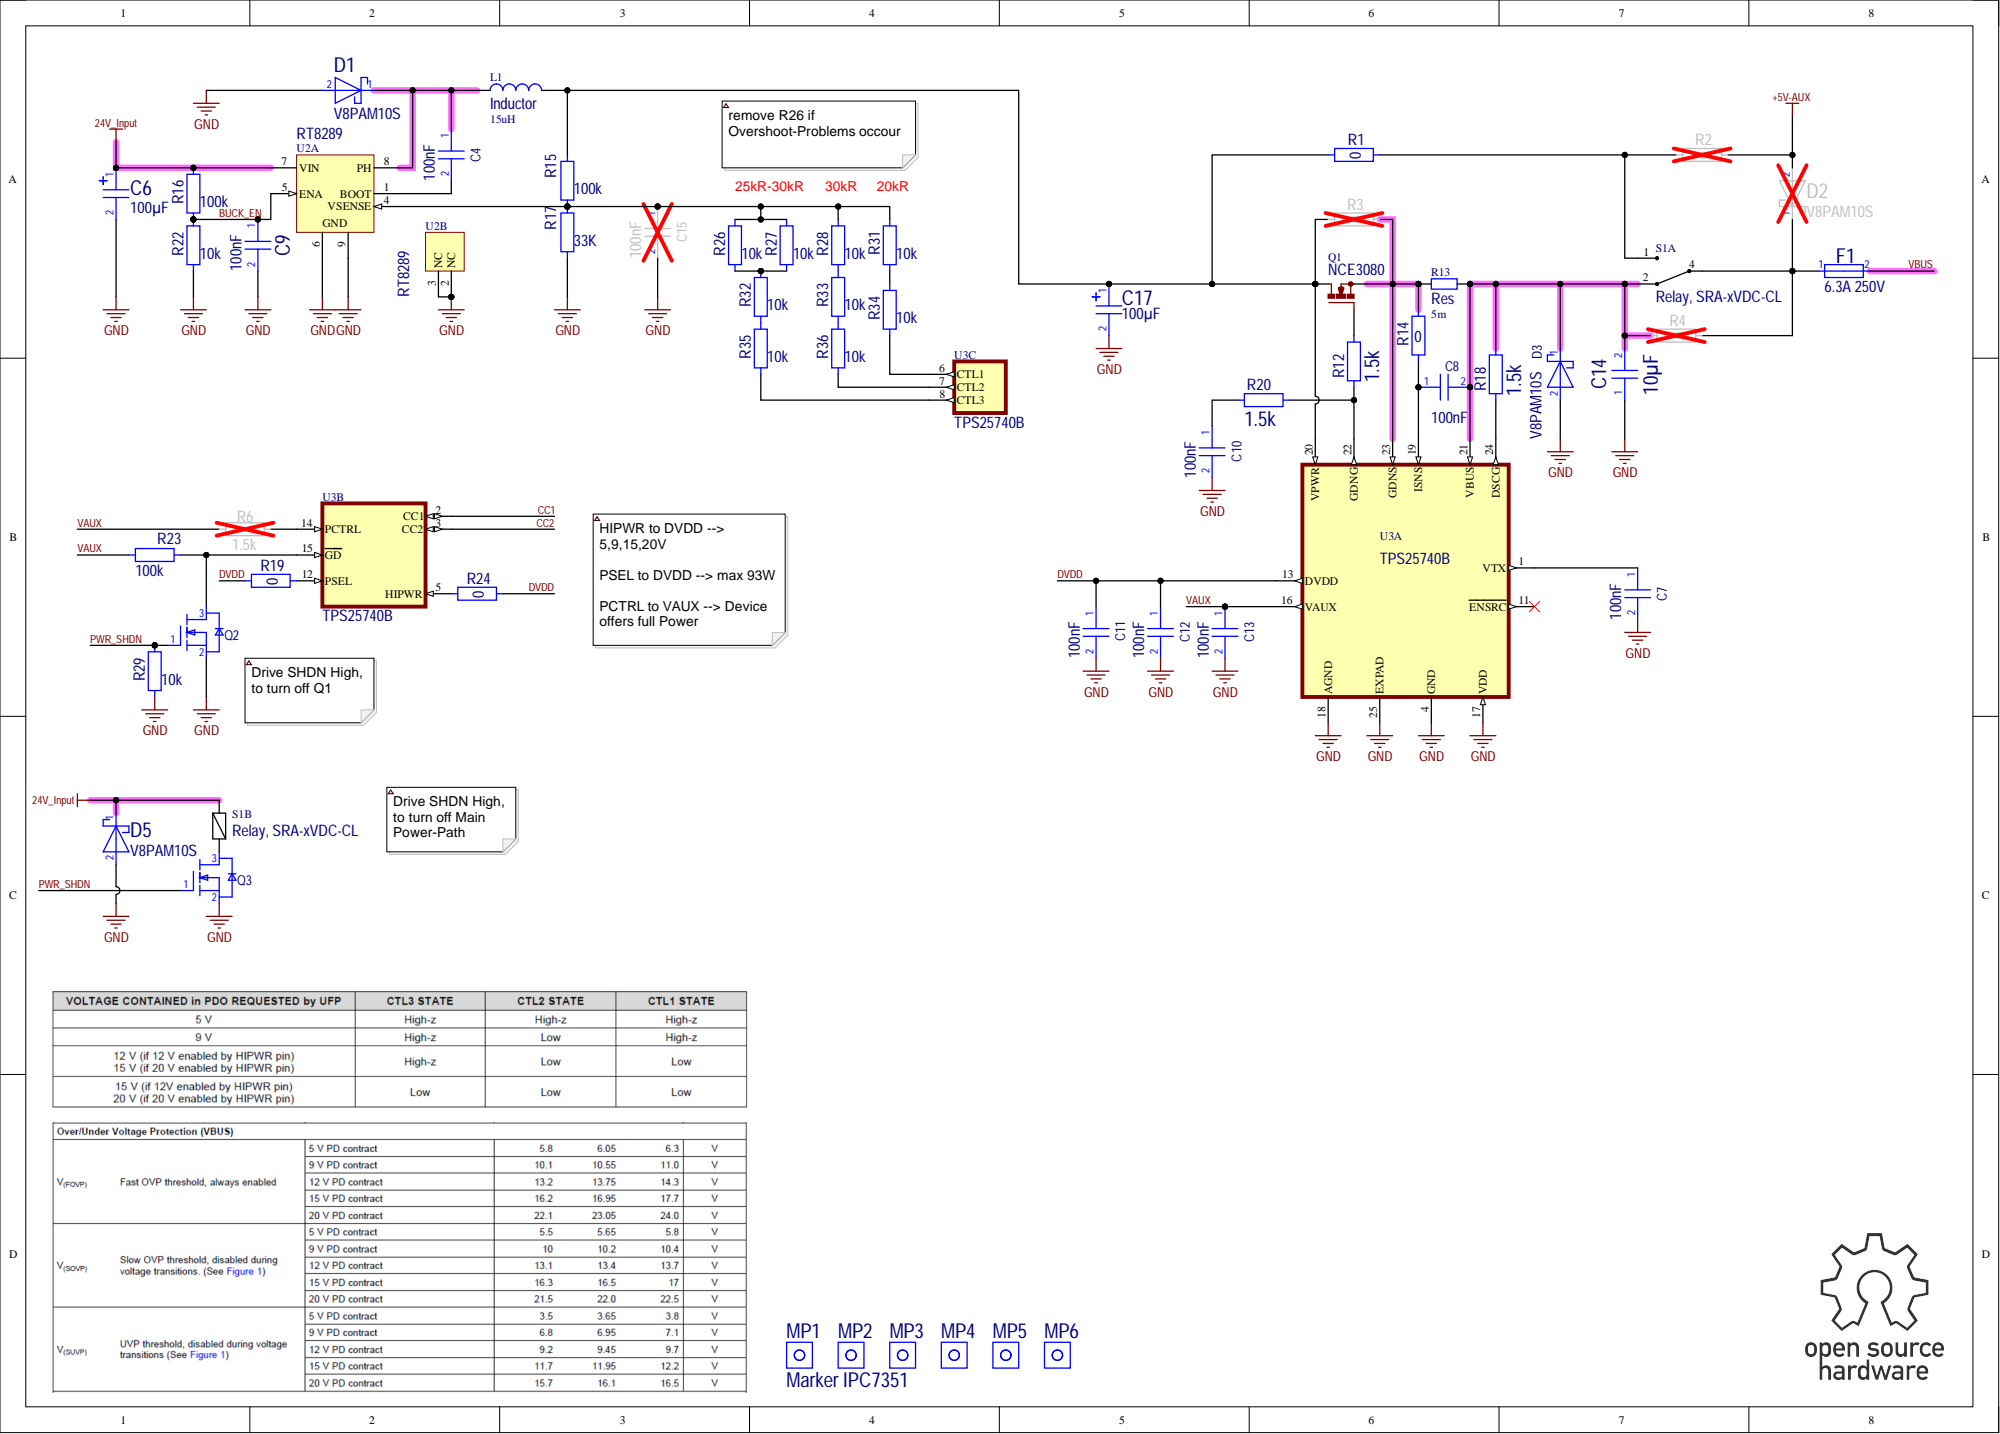
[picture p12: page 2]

PSEL to DVDD --> max 93W

PCTRL to VAUX --> Device
offers full Power

Drive SHDN High,
to turn off Main
Power-Path

Relay, SRA-xVDC-CL

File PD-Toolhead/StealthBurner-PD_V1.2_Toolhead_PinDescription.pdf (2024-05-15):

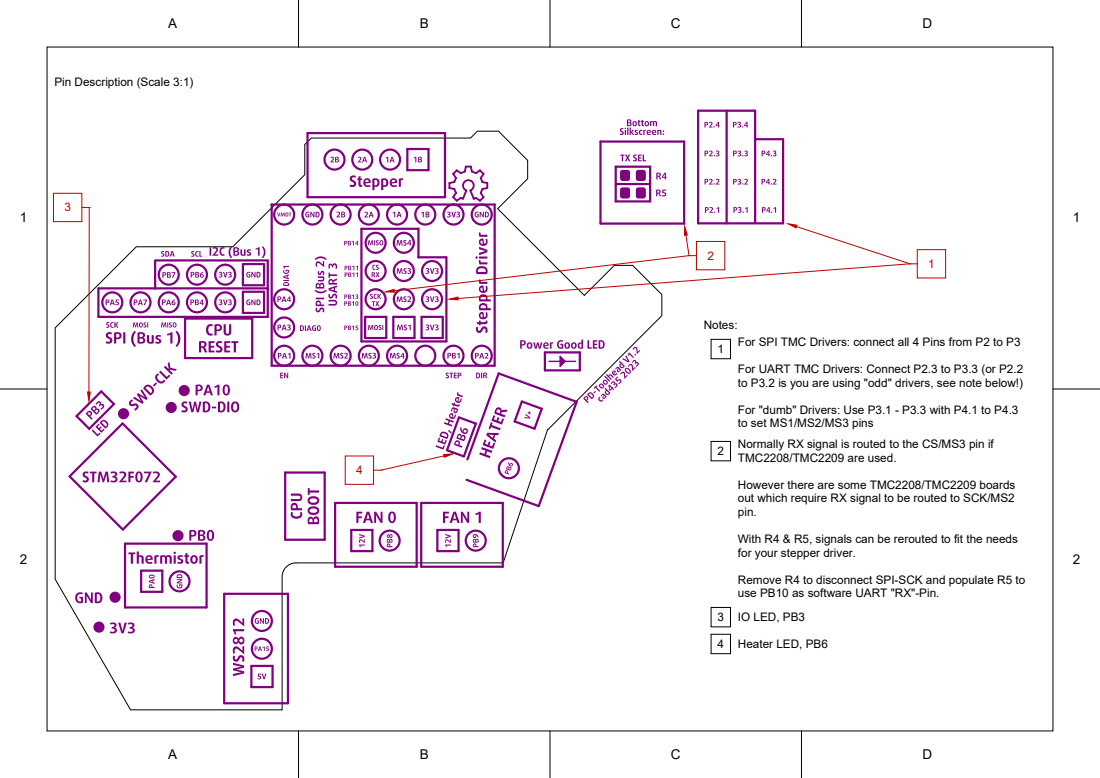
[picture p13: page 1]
4 Heater LED, PB6

Pin Description (Scale 3:1)

Notes:
For SPI TMC Drivers: connect all 4 Pins from P2 to P3
For UART TMC Drivers: Connect P2.3 to P3.3 (or P2.2
to P3.2 is you are using "odd" drivers, see note below!)

For "dumb" Drivers: Use P3.1 - P3.3 with P4.1 to P4.3
to set MS1/MS2/MS3 pins
Normally RX signal is routed to the CS/MS3 pin if
TMC2208/TMC2209 are used.

However there are some TMC2208/TMC2209 boards
out which require RX signal to be routed to SCK/MS2
pin.

With R4 & R5, signals can be rerouted to fit the needs
for your stepper driver.

Remove R4 to disconnect SPI-SCK and populate R5 to
use PB10 as software UART "RX"-Pin.
3 IO LED, PB3

Realistic View

View from Top side (Scale 3:1)

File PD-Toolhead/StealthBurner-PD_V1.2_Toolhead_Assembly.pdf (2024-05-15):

A

B


Top SMD/THT (Scale 2:1)

Bottom SMD/THT (Scale 2:1)

1 | 1


1 | 1

# Top THT (Scale 2:1)


1 | 1

# Realistic View


2 | 2
3 | 3
4 | 4

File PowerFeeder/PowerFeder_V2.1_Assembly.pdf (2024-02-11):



Realistic View

View from Top side (Scale 2:1)

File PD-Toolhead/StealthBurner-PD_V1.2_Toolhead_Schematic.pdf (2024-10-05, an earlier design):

C10



Normally RX signal is routed to the CS/MS3 pin if
TMC2208/TMC2209 are used

However there are some TMC2208/TMC2209 out
which require RX signal to be routed to SCK/MS2 pin

With R4 & R5, signals can be rerouted to fit the needs
for your stepper driver.

Remove R4 to disconnect SPI-SCK and populate R5
to use PB10 as software UART "RX"-Pin

For SPI TMC Drivers: connect all 4 Pins from P2 to P3

For UART TMC Drivers: Connect P2.3 to P3.3 (or P2.2 to P3.2 is you are using
"odd" drivers, see note above!)

For "dumb" Drivers: Use P3.1 - P3.3 with P4.1 to P4.3 to set MS1/MS2/MS3 pins

st Modific; ation:; Docum; ent: PD-Sink.SchDoc; Proje; ct: PD-Toolhe; ad.PrjPc; ariant: [No V; ariations; VBU; VBUS R10; LED-0603

# Inductor ⁴.7uH/1.7A/

D1


5V will actually be around 4.8V

This is desired, as Neopixels have a high level of
Vdd. If we have a 3.3V signal, than we can only
afford 4.7V level signal (
with a 5V supply and a 3.3V signal, so I think 4.8V is
fine.)

most of the time it'll work also

Need a tradeof between physical size and practicability
here as the PCB is already packed.

In case it does not work, tweak R25, R26 and R27

## FAN0

## FAN1


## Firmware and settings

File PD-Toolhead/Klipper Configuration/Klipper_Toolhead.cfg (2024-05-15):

## "MF0" is short for "Multi Feeder 0"
## note that only the lines which are relevant pins for the PD-Hardware PCB are written down!


[mcu MF0]
serial: /dev/serial/<path here>

[extruder]
step_pin: MF0:PB1
dir_pin: MF0:PA2
enable_pin: !MF0:PA1

[...]

heater_pin: MF0:PB5

[...]

sensor_pin: MF0:PA0

[...]

# SPI bus definitions see https://github.com/Klipper3d/klipper/blob/master/src/stm32/spi.c

[tmc2130 extruder]
cs_pin: MF0:PB11
#   The pin corresponding to the TMC2130 chip select line. This pin
#   will be set to low at the start of SPI messages and raised to high
#   after the message completes. This parameter must be provided.
#spi_speed:
#spi_bus: spi2
spi_software_sclk_pin: MF0:PB13
spi_software_mosi_pin: MF0:PB15
spi_software_miso_pin: MF0:PB14

[...]

# fan for the Extruder Heatsink
[heater_fan MF0_HFan]
pin: MF0:PB9
[...]
hardware_pwm: false
shutdown_speed: 1.0

# Partcooling Fan on Extruder 0
[fan_generic MF0_PFan]
pin: MF0:PB8
hardware_pwm: false
cycle_time: 0.08 #seems to be a good time to not get to much fan noise


# Status LED, just a single green LED on the board (see Pindescription PDF)

[led _MF0_StatLed]
white_pin:
    MF0:PB3
cycle_time: 0.1
initial_WHITE: 1.0
#   Sets the initial LED color. Each value should be between 0.0 and
#   1.0. The default for each color is 0.


#Neopixel LEDs connected to the LED-Header
[neopixel MF0_leds]
pin: MF0:PA15

[...]


# this is the ADXL if connected to the Toolhead PCB
[adxl345]
cs_pin: MF0:PB4
spi_bus: spi1
axes_map: z,y,x # this would apply for Stealthburner Toolhead

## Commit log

2023-05-28 Initial Upload
    [PowerFeeder_X4_Panel.GBL, PowerFeeder_X4_Panel.GBO, PowerFeeder_X4_Panel.GBP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]
2023-06-11 Corrected Gerber
    JLC didn't want to manufacture at first, some via diameter to small, corrected
    [PowerFeeder_X4_Panel.GBL, PowerFeeder_X4_Panel.GBO, PowerFeeder_X4_Panel.GBP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]
2024-02-11 Updated to new Version
    Toolhead V1.1
    Feeder V2.1
    [PD-PowerFeeder_Panel.GBL, PD-PowerFeeder_Panel.GBO, PD-PowerFeeder_Panel.GBP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]
2024-02-11 Updated Klipper Configuration
2024-02-11 Klipper.md --> Klipper.cfg
    [Klipper_Toolhead.cfg]
2024-02-12 Added 3D-Data
    [USB_Cable_Holder.f3z]
2024-05-15 Added new Version of toolhead
    Added the new Version of the toolhead
    - Complete Relayout for improved EMI rejection
    [Klipper_Toolhead.cfg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]
2024-05-15 Added JLCPCBA.xls for toolhead
    [V1.2_JLC_PCBA_CPL.xlsx]
2024-05-15 Updated JLCPCBA for Toolhead
    [V1.2_JLC_PCBA_CPL.xlsx]
2024-05-16 Updated Panel
    Make Panel bigger
    Added Mousebites for easier depanelisation
    [PD-Toolhead_Panel.GBL, PD-Toolhead_Panel.GBO, PD-Toolhead_Panel.GBP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]
2024-10-05 Replaced R7 and R8 with 0R (100R was too much for some setups)
    [CPL-PD-Toolhead(V1.2).xlsx, V1.2_JLC_PCBA_CPL.xlsx]
2025-08-03 Replaced IRFH3702 with CSD17552Q3A
    [JLC_PCBA_BOM-PD-Toolhead(V1.3).xlsx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]
